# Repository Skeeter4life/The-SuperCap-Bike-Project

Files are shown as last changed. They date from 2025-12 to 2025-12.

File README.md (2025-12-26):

# SuperCAP V1 is Complete, and Deprecated in Light of V2.

## The Idea

I wanted an electric bike with a more dynamic feel than the typical e-bike; one in which you wouldn’t be able to get away with constantly cruising at 30km/h with minimal effort. I wanted an e-bike that had a sense of “sportyness”, quick, instantaneous acceleration. I also wanted the sence of scarcity. The goal was to have an e-bike that could get me up a hill, yet had limited capacity, such that it still enticed me to get some proper exercise. A super-capacitor based accumulator is perfect for this, as they have reduced charge density, and generally are able to source and sink signifigantly more current with less problems then for instance, a Lithium Ion battery. The accumulator would consist of two 12V 500F supercapacitor banks, which could be connected in parallel or in series. The electronics will be powered independently with a 12V battery.

> [!Note]
> These were my honest initial thoughts going into the project. The practical implications of this will be described in [Things That Went Wrong](#things-that-went-wrong)
>
> Inspiration  from [Tom Stanton's "Super Capacitor Bike"](https://www.youtube.com/watch?v=V_f8Q2_Q_J0) video on YouTube.

> [!Note]
> I am going to focus my discussion here on the hardware. There is so much to talk about regarding the firmware, but to keep this documentation of my learning as condensed as possible, I will rely on my comments I made in my code for you to interpret. 

> [!IMPORTANT]
> The uploaded schematic is original, and has NOT been updated to reflect any of the changes mentioned below. I have decided to use that time towards V2.

## Things That Went Right

### 1. Dedication and Perseverance
It is very important to know that I have had no formal education on any of this (as of 2025/11/08). I have not yet taken any course that explains the practical applications and operation of a diode, MOSFET, or any nonlinear device. I spent my evenings teaching myself as much as I could before falling asleep. I spent as much energy and time as I could during my free time (sometimes putting off homework…) to work on my project. I need to emphasize that I was extremely dedicated and determined to get this project in a usable state. I am only now taking ECE 370 this term, which sheds light on the operation of electromechanical devices.

I also did not have any adequate equipment when going into this project. I did not let that stop me, but reflecting back on it, it would have made a world of difference. Please, behold, the setup I had in my landlord’s garage while I was on co-op:

Setup-landlord

### 2. Decision to use a 2 Layer PCB for Prototyping
If you looked at this project in the early stages of development, you may remember that I chose the 2-layer PCB primarily due to cost and “EMI was not my primary concern” (Okay, that was really silly to say. Hindsight is 20/20). This will be briefly addressed in [Things That Went Wrong](#things-that-went-wrong), to an extent, as far as I can explain; I am not even close to being able to design for EMC. This choice ended up being quite beneficial as I needed to cut and re-route many, many traces on my PCB.

### 3. I had the Right Idea
I understood the principles of what needed to happen, and how it could be achieved. While some components could definitely have been chosen better ([Things That Went Wrong](#things-that-went-wrong)), atleast they were the correct type of components. I understood that I needed 3 half bridge circuits, one per phase. I understood that a P-type MOSFET typically has a higher $$R_{ds ON}$$ than an N-type MOSFET. I understood that I needed some sort of circuit to keep $$V_{gs}$$ in the saturation region as the high-side N-type MOSFET began to conduct. I understood the principles of decoupling capacitors, I choose appropriate values and kept them as close as possible to the IC. I even put bulk capacitance throughout my circuit (could have done a better job, but I will still give myself props). Furthermore, I even tried to put some (questionable at best) circuit protection features. This prototype defiently would not even be workable if I did not execute those parts properly.

## Things That Went Wrong 

As mentioned in [Things That Went Right](#things-that-went-right), I was completely self taught. I wish I had the time to learn absolutely  everything, tinker with each component for way longer, but things have been way too busy. Part of me just wanted this project done for the next co-op search and to finish my schoolwork, so, I rushed. There are many design flaws, logic errors, and inconsistencies throughout the project; but to keep this section concise and readable, I am going to limit myself and only discuss in detail the three most signifigant design faults. 

### 1. No ISP

This ultimately came down to an extremely silly error: I used 1.0mm header footprints, not 2.54mm. I had the pins to program the ATMEGA328P over UART, but due to their size, spacing, and my available tools, it made it way too finicky to solder on a bodge fix. As such, I had to remove the ATMEGA328P and place it onto a breadboard each time to reprogram, which is a mistake I do not want to repeat (The 28-PDIP IC defiently was not designed for constant insertion and removal). Additionally, my screw terminals were missing the SPI line MISO and a connection to the ATMEGA328p's RESET pin, so I had to repeat the process of removing the microcontroller each time to use DebugWIRE or change a fuse bit.

### 2. Chosen Components and Thermal Performance

I mentioned this before in [Things That Went Right](#things-that-went-right), that I did my best to figure out what all of the specifications meant on the datasheet, but it ultimetly meant that some paramaters got neglected. It is crazy to say, but sometimes I got so hooked after learning something nitty-gritty about a component, that I got excited and put it on my BOM, and completely neglected some other paramaters. For instance, let's take a look at my choice for using the onsemi 1N4148 signal diode [^5] used in the bootstrap circuit for the IR2104 [^30] (mistakenly, it has a schottky diode symbol on my schematic). 



The first thing that pops out to me is the absolute maximum recurrent peak forward current rating of 400mA. I likely exceed this during the initial C<sub>boot</sub> charging transient, as I do not have a current-limiting resistor in series with the diode. Below entails an analysis to see the current drawn at t = 0:

<p align="center">
  
$$ I(t) = I_oe^{\frac{-t}{\tau}} \text{ (A)}$$

$$ I(0) = I_o = V/R_{eq} \text{ (A)}$$

$$R_{eq} = R_{diode-eff} + Capacitor_{ESR} + Sourse_{ESR} + Parasitic_{ESR}\ (Ω)$$

Assumption: $$R_{diode-eff} = 0$$
I am assuming that the diode is an ideal diode to get an upper-bound for the peak surge current. There would be a forward voltage drop and some equivalent effective resistance at that current, but the datasheet does not provide any information as soon as the current $$> 800mA$$.

$$Capacitor_{ESR}: \ \approx \text{15 (mΩ)}$$

$$Sourse_{ESR}: \ \approx 8 * 0.2 = 1.6 \text{ (Ω) (8 1.5V AA alkaline batteries in series)} $$

$$Parasitic_{ESR}: \text{ The resistance of a trace with 1.5mm width, 0.6mm length, } 1 \frac{oz}{ft^2}, \text{ at } 25^{\circ}C \approx 0.194 \text{ (mΩ).}$$

IR2104 I/O impedence assumed neglegable.

$$R_{eq} \approx 1.62 \text{ (Ω)}$$

$$= 12/1.62 = 7.4 \text{ (A)}$$

</p>

However, the surge current decays quickly as seen at three time constants:

$$ I(t) = I_oe^{\frac{-t}{\tau}} \text{ (A)}$$

$$ I(3\tau) = \frac{I_o}{e^3} = V/(R * e^3) \text{ (A)}$$

$$= 12/32.54 = 369 \text{ (mA)}$$

Now let's take a quick look at its thermal characteristics:



It is quite likely I exceeded the power dissipation rating aswell. Now it is true that this tiny diode was dissipating power for a tiny amount of time: 

$$5\tau \text{ (s)} $$
$$\text{Voltage } C_{boot} = 0.993(12) \text{ (V)}$$
$$ = 5*RC_{boot} $$
$$ \text{= 5 * 1.62 * 0.000001 = 8.1 (us)} $$

So, it almost makes some sense that it did not explode as soon as I tried using my bootstrap circuit. The instantaneous power is quite high, but the average over time with the frequency I was switching the MOSFETs (~10kHz: a limitation of the timers in the ATMGEA328P) is acceptable. Nevertheless, its vital to design a system that meets all absoloute maximum ratings, with a buffer. 

Furthermore, The 1N4148 diode has a non-negligable forward drop when sinking even uA of current. The highside is still being driven at an appropriate $$V_{gs} \approx 11V$$. However, this is still worth additional consideration moving forward. 

<p align="center">

</p>

On the other hand, I do want to briefly go over the fact that the 1N4148 diode's maximum repetitive reverse voltage, reverse leakage current, reverse recovery time and junction capacitance specifications are appropriate for this use case. When the IR2104's high side gets switched on, the 1N4148 is going to need to handle a reverse voltage of 24V. It is rated for 100V, so that is a win. The only inductance in the loop is from the parasitics from the traces, so $$L \frac{di}{dt}$$ is small, and thus, the switching transient will remain well below 100V. The 1N914 has a reverse leakage of 0.025uA when $$V_R = 20V$$, which means I am not going to get too heavy in the math, but to my understanding, low leakage current means the bootstrap capacitor will stayed charged for longer, and the low junction capacitance/fast recovery time minimizes the ringing/switching loss, which is good.

I think that covers everything for the bootstrap diode. My math definitely overestimates the stress on the diode through my ideal diode simplification, but all in all, this is a better analysis than what I had before. If I were to choose any other component to replace it, under the following assumptions:

- Able to handle a repetitive surge forward current of a of couple amps, allowing for some $$C_{bs}$$ to be charged in the order of a few nanoseconds,
- Required reverse votlage of 24V * 2 (accumulator in series, 2* to give room for transients),
- Fast recovery time, minimizing losses
- Low leakage current
- Low forward voltage drop

I would choose [this Schottky diode](https://www.digikey.ca/en/products/detail/taiwan-semiconductor-corporation/SSH210H/18718578).

### 3. The MCP23017

To begin, a better choice would have been an I/O expander with a protocol capable of running at a higher baud rate, like SPI. One of my greatest mistakes in this project was not considering the timing implications of using the I/O expander, the MCP23017. I wired the digital output of hall effect sensors, break switches, and even the fault LED to the I/O expander. These are all things that I would want directly connected to the MCU. The hall and break switch interrupts are extremely high priority. The MCP23017 has two interrupt lines, multiplexed across the two ports, dedicating 8 independent pins per port. The designers of the MCP23017 added a register that holds the flags for the pins that raised an interrupt; however, this creates a major performance issue in my case. It is required to read the “interrupt captured register” before the interrupt line state resets. Every interrupt required a full read cycle, which is a major performance issue: the I2C bus for this application is unsafe, unreliable, and causes atleast a 10 times delay of the MCU’s ability to process subsequent interrupts. I originally did not consider this delay. As a result, the motor would stall at speed; the hall state would be read too late, and a phase with a lower index would be applied.

I did a brief analysis of how much time I had between subsequent hall states. Below is an image of the motor rotated to one of its commutation states:

<p align="center">

</p>

The radius I measured to be about $$50mm$$. Using a protractor, the rotor only needs to turn $$\approx 1^\circ$$ before the hall effect sensor changes state. The calculus for measuring the arc length of a circle has been done and is well known: 

$$L = 2\pi r \frac{\Theta}{360}$$

$$L \approx 0.87 \text{ mm}$$

Below is an image of the fastest possible I2C read transaction with the ATMEGA328P, 

(I consider this a feat, I am quite proud of this. Bit rate of ~1MHz (2f).

<p align="center">
SDS804X_HD_PNG_9
</p>

A bit of algebra yields the absolute maximum I2C interfaced motor speed:

$$\frac{0.87*10^{-3}}{v} \le (67.8 * 10^{-6}) + ISR_{execution} $$

$$\text{For simplicity (was not measured) } ISR_{execution} = 0$$

$$ v \le 12.8 \frac{m}{s} \approx 45 \frac{km}{h}$$

If you are familiar with I2C, you would have noticed that the ACK bit had a suspiciously high voltage. At the speeds I was running it, it would occasionally glitch and the MCP23017 would not be able to pull the ACK bit low, resulting in a NACK bit. Using stronger pull-up resistors did not make a noticeable difference. I was pushing the limits of my I2C bus, and the AMTEGA328p’s TWI timing capabilities; it is officially only rated for a 400kHz transfer speed.

So, when doing my tests, I reduced my I2C baud rate from 1MHz to 400kHz. Here is a video demonstrating the motor stalling (video is heavily compressed to meet 10MB upload limit, apologies):

https://github.com/user-attachments/assets/7227a615-8b7e-4955-889b-a2fbc8cb35df

> [!Note]
> I bought the oscilloscope and tools after my co-op. The PCB was designed and built at this time.

Revisiting the first note, the main flaw with this supercapacitor bike idea is that none of my electronics or even my motor is rated for large currents. I don’t have the datasheet for my motor (I asked, but, the seller wouldn’t give it to me), but the use of 16-gauge stranded aluminum phase wires was enough for me to realize that sinking anything around 10A was a bad idea. The other key flaw with my original intuition was I could simply just decided not use the e-bike’s power assist by turning it off, nullifying the entire supposed benefit of the limited capacity. Some sort of hybrid capacitor-battery approach would be better suited (Lithium-ion Capacitors), whilst keeping the spirit of the project.

### Honerable mentions:

**1. Incorrect Wiring of the IR2104's**
  - All shutdown pins were tied together.
    
**2. Completely Inconsistent Labels, Silkscreen, and Ordering**
  - MCP23017's INTA is labeled as INTB, and vice versa.
  - U2 has silkscreen "U1", U1 has silkscreen "U2".
  - U1, U2, and U3 are not organized in a sequential order.
  - Phase1, Phase2, and Phase3 connections are not listed sequentially.
    
**3. Wrong Footprints**
  - Barrel Jack (PJ-002AH) FootPrint: A lesson to not put complete trust into the EDA models found on DigiKey. I had ignored KiCAD's DRC violation that the hole clearance was 0mm, shorting supply and ground.
  - Relay (AWHSH105D00G) Footprints: Wrong footprint, one through-hole pad is entirely missing.
    
**4. Circuit Protection Elements Doing More Harm Than Good**
  - I have diodes on my 5V, 3.3V lines; this caused the voltage to be too close to $$V_{min}$$ of the MCP23017's defined logic levels.
    
**5. Schematic is Unorganized and Difficult to Read**
  - Organizing a schematic takes expereince.
    
**6. No (initial) Consideration of the I2C Bus Pull Up Resistors**
  - I arbitrarily chose 10kΩ, which I later had to add 2.2kΩ resistors in parallel.
    
**7. Series/Parallel Switching**
  - To keep this brief, I feel that this is still a good idea (assuming software and hardware has been implemented to ensure it is safe to do so), but there needs to be a major revision to what I have on my schematic. The most prominent issue is the relays. EMI was such an issue on my PCB that under high load, or some sort of grounding issue, the relay(s) would toggle. If I were to ever choose to use relays, I would need to do proper analysis to ensure that under no circumstances can they spuriously toggle. Also, I would need to add some sort of current sensing to ensure that I am still operating within the contact ratings. Another major concern is the potential for inrush currents. It is quite plausible to have one capacitor at a slightly different potential than the other. In addition to the current sensing, there would be a need for some sort of regulator to handle transients.
    
**8. I Did Not Add Any Real Way to Charge the Accumulator**
  - I had the original idea of just taking the accumulator off, hooking it up to a DC power supply etc, but a nice luxury would be to be able to plug it in directly to a wall outlet.

**9. The PCB Could Have Been Designed Better**
- I rushed the production of the PCB, and I believe I could have done a better job routing tracks and organizing the components. The ground and power planes are excessively fragmented, resulting in poor current return paths and increased noise.
- The board already exceeds the 100x100mm pricing tier. Surface mount components would have reduced cost and complexity. There is an excessive amount of signal via's, traces bending around IC's with sharp corners, etc., that could have been avoided with better component placement, organization and additional board space. Additionally, I would have been able to better separate the sensitive digital electronics from any high power tracks and the power plane. 
-  I could have improved thermals and reduced capacitive coupling with the use of thermal and stitching vias. Furthermore, I should have kept the high-frequency SPI, I2C, and the crystal oscillator tracks as isolated, short, and straight as possible.
    
**10. No Pull-Down Resistors on Some MOSFETS**
  - I did not add any pulldown resistors on the half-bridge FET's. When the IR2104 driver was in a HIGH-Z state, capacitive coupling caused $$V_{gs}$$ to increase, just enough to start to put the FET into conduction. The only reason I noticed this is because some FET's got mysteriously hot.
    
**11. Bootstrap resistors, Gate Resistors Chosen Arbitrarily**
  - To be fair to myself, I had no equipment at the time to be able to emperically measure the effects of one gate resistor vs. another. However, these are the sorts of things you can get an upper and lower bound for through calculations, which I did not do.

There are definitely some more things I did not write, might have missed/don't fully understand yet. All in all, I will conclude this section here, as I believe it highlights the core of my learning. If there is something here you would like to talk about, feel free to in an interview or in the issues section.

## The Outcome

I consider this project to be a success. I had a lot of fun releasing some magic smoke. In all seriousness, I got some incredibly valuable hands on experience designing my first ever prototype for quite an ambitious project. I essentially have a fully functional BLDC motor controller. Below, I posted an uncompressed video of one of the "top speed" runs of my motor (or at least, as fast as I can go without feeling worried about tripping my room's breaker or melting those aluminum wires).

<div align="center">
  <video src="https://github.com/user-attachments/assets/f553f186-a5bf-4020-b508-6ff7d6a13e7c">
</video>
</div>

(Note: I was using a higher duty cycle than the I2C test) Below is an image of the bottom my PCB with the "bodge" fixes:

<p align="center">
PCB_Bodge
</p>

Below is a top down view of the PCB:

<p align="center">
PCB_Bodge
</p>

## What I Will do in Version 2

Version 2 will address all of the aforementioned issues. Here are my initial thoughts and goals:

- I will switch to a more capable microcontroller. I am definitely looking into STM32, I need something with a higher instruction throughput, greater word size, ideally has an FPU, variable frequency timers (capable of field-oriented control), and more I/O. Everything should be able to interface directly to the MCU. I need to include relevant ISP modules.
- I need to switch to a larger 4-layer or 6-layer PCB, and improve my designs layout and organization. I will attempt to reduce EMI: I should have dedicated uninterrupted ground planes, stitching vias, and use best practices to keep high-frequency traces short and straight. I also need to keep thermals in mind.
- I will use heat sinks where needed and thermal vias; stitching the top and bottom copper planes.
- I will perform power and EMI analysis (I will be switching to Altium).
- I will design a proper back-EMF circuit for regenerative braking; power dissipation in body diodes will be high and inefficient.
- I will switch to a Li-ion capacitor-based accumulator. I will design a circuit to allow for charging directly from a standard wall outlet. This of course requires safe charging/protection features.
- I will design a current and voltage monitoring system to ensure the motor is operating safely, and to take action when it is not.
- I will aim to drive a 500W BLDC motor (a motor *with* a datasheet). I will consider the motor's characteristic curves to maximize power output and efficiency.

## Bill of Materials

Ceramic Capacitors: 
- 0.1uF x 7 [^1], 
- 0.33uF x 2 [^2],
- 1uF x 3 [^3]

Electrolytic capacitors: 
- 10uF x 4 [^4]
  
Diodes:
- 1N4148 x 3 [^5], 
- 1N5819 x 5 [^6]

LEDs: 
- 5.0mm THT x2 [^7]

Fuse: 
- 0225002.MXP x1 [^8], *Note:* Never implemented or tested.
- F4658-ND x 1 [^9] *Note:* Never implemented or tested.

Sockets & Pins: 
- 1x01 1.00mm Vertical Male Pin x 5 [^10],  *Note:* Never purchased, implemented or tested.
- 8 Dip 7.62mm Socket x 5 [^11],
- 16 Dip 7.62mm Socket x 1 [^12], 
- 28 Dip 7.62mm Socket x2 [^13] 

Barrel Jack: 
- PJ_002AH x 1 [^14]

Relays: 
- AWHSH105D00G x 2 [^15]

MOSFETS:
- IRFZ44N x 7 [^16], 
- GT065P06T x 1 [^17]

Resistors: 
- 0Ω, 10Ω, 220Ω, 10kΩ, 22kΩ Resistor Kit: [^18]

Terminals: 
- 1988804 x 1 [^19], 
- 1988817 x 2 [^20], 
- 1190363 x2  [^21], 
- 1988862 x 3 [^22]

Microprocessors: 
- ATMEGA328P x 1 [^23]

Crystal Oscillator: 
- MXO45HS-3C-20M000000 x 1 [^24]

GPIO Expander: 
- MCP23017 x 1 [^25]

Button: 
- TS02-66-50-BK-160-LCR-D x 1 [^26]

MOSFET Gate Driver: 
- UCC37324P x 1 [^27] *Note:* Never implemented.

Darlington Transistors Array: 
- ULN2003 x 1 [^28]

Digital Potentiometers: 
- MCP4151 x 1 [^29]

Half Bridge Drivers: 
- IR2104 x 3 [^30]

Linear Regulators: 
- L7805 x1 [^31], 
- L78L33ACZ x1 [^32] *Note:* Never purchased, implemented or tested.

Hall Effect Sensors: 
- TMAG5213AGQLPG x 3 [^33]

Switches: 
- 2057-SW-R-K1-A-ND x 1 [^34] 

Subtotal: **$ 146.17 CAD** (as of 2025/11/08)

## Schematic and PCB

### Schematic:  

  To reduce image congestion, please clone the repository and access the schematic on KiCAD version 8+.

### PCB:

<div align="center">

PCB_Components
PCB_Traces

</div>

## My Policy on the Use of AI

I fully acknowledge the emergence of AI and how useful it can be as a tool. However, I am also fully aware that there are negative consequences for the overreliance on AI. That being said, I take pride in the fact that I fully wrote all core components of my code; the same is said with the hardware portion. If you look carefully through my program, you will be able to pick up my quirks and coding style. However, I did not completely abstain from using AI. I would ask ChatGPT to help me with a concept, look up what register to use, or how to perform some sort of function. I used ChatGPT as a tutor, not as a tool to do everything for me. It is worth mentioning that ChatGPT is not perfect. For instance, I pasted some code into ChatGPT and asked “what interrupt vector do I use here?”, to which ChatGPT said “INT_vect” instead of “INT0_vect”. A very minor mistake, but I didn’t understand what was wrong, and I was using no other resources. I was then confused for an hour about why my ISR never executed. It was confidently incorrect the entire time we went through the debugging process; I was overreliant, and ChatGPT was more concerned with my wiring setup than realizing the interrupt vector was wrong. So, to summarize, AI is a great tool, and there are parts of my code where AI helped me out, but I never just blindly copied and pasted big chunks of its work for a full feature. I spent countless hours going through datasheets (I feel like I am one of the very few people who have read nearly the entirety of the ATMEGA328P datasheet), did my best to find information myself, and then, if all else failed, I would have asked ChatGPT for some advice.

<div align="center">

  ***Thank you!***

</div>

Hall-Effect-Sensor-Replacement

## Links

[^1]: https://www.digikey.ca/en/products/detail/kemet/C322C104M5U5TA/818107
[^2]: https://www.digikey.ca/en/products/detail/kemet/C330C334M5R5TA/6562403
[^3]: https://www.digikey.ca/en/products/detail/kemet/C330C105K5R5TA7301/3726162
[^4]: https://www.digikey.ca/en/products/detail/cornell-dubilier-knowles/106CKE400M/5410625
[^5]: https://www.digikey.ca/en/products/detail/onsemi/1N4148/458603
[^6]: https://www.digikey.ca/en/products/detail/stmicroelectronics/1N5819/1037326
[^7]: https://www.digikey.ca/en/products/detail/marktech-optoelectronics/MT4118-HR-A/4214622
[^8]: https://www.digikey.ca/en/products/detail/littelfuse-inc/02540101Z/553102
[^9]: https://www.digikey.ca/en/products/detail/littelfuse-inc/0225002-MXP/777781
[^10]: https://www.digikey.ca/en/products/detail/samtec-inc/TS-101-T-A/1105493
[^11]: https://www.digikey.ca/en/products/detail/te-connectivity-amp-connectors/1-2199298-2/5022039
[^12]: https://www.digikey.ca/en/products/detail/on-shore-technology-inc/ED16DT/4147596
[^13]: https://www.digikey.ca/en/products/detail/adam-tech/ICS-328-T/9832859
[^14]: https://www.digikey.ca/en/products/detail/same-sky/PJ-002AH/408446
[^15]: https://www.digikey.ca/en/products/detail/amphenol-anytek/AWHSH105D00G/16721986
[^16]: https://www.digikey.ca/en/products/detail/umw/IRFZ44N/24889964
[^17]: https://www.digikey.ca/en/products/detail/goford-semiconductor/GT065P06T/18088004
[^18]: https://www.digikey.ca/en/products/detail/sparkfun-electronics/COM-10969/14671649
[^19]: https://www.digikey.ca/en/products/detail/phoenix-contact/1988804/950892
[^20]: https://www.digikey.ca/en/products/detail/phoenix-contact/1988817/950893
[^21]: https://www.digikey.ca/en/products/detail/phoenix-contact/1190363/14680902
[^22]: https://www.digikey.ca/en/products/detail/phoenix-contact/1988862/950898
[^23]: https://www.digikey.ca/en/products/detail/microchip-technology/ATMEGA328P-PN/2357094
[^24]: https://www.digikey.ca/en/products/detail/cts-frequency-controls/MXO45HS-3C-20M000000/1801871
[^25]: https://www.digikey.ca/en/products/detail/microchip-technology/MCP23017-E-SP/894272
[^26]: https://www.digikey.ca/en/products/detail/same-sky-formerly-cui-devices/TS02-66-50-BK-160-LCR-D/15634352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
[^27]: https://www.digikey.ca/en/products/detail/texas-instruments/UCC37324P/571464
[^28]: https://www.digikey.ca/en/products/detail/stmicroelectronics/ULN2003A/599603
[^29]: https://www.digikey.ca/en/products/detail/microchip-technology/MCP4151-103E-P/1874217
[^30]: https://www.digikey.ca/en/products/detail/infineon-technologies/IR2104PBF/812198
[^31]: https://www.digikey.ca/en/products/detail/stmicroelectronics/L7805CV/585964
[^32]: https://www.digikey.ca/en/products/detail/stmicroelectronics/L78L33ACZ/1038304
[^33]: https://www.digikey.ca/en/products/detail/texas-instruments/TMAG5213AGQLPG/22531584
[^34]: https://www.digikey.ca/en/products/detail/adam-tech/SW-R-K1-A/15284469

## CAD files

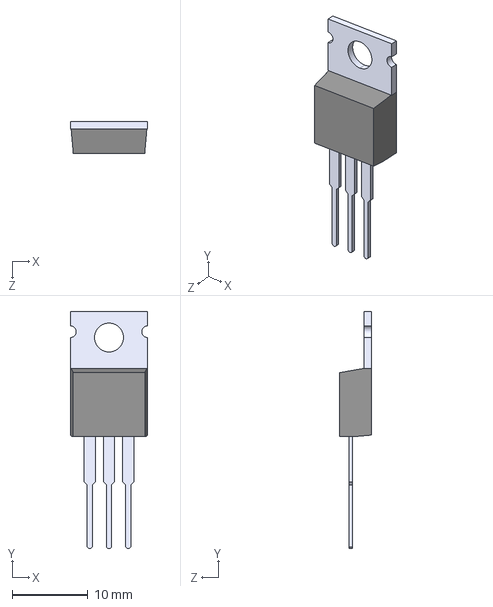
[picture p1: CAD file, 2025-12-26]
Hardware/Libraries_Kicad/Footprints/IRFZ44N/IRFZ44N.step
10.2 x 31.2 x 4.19 mm

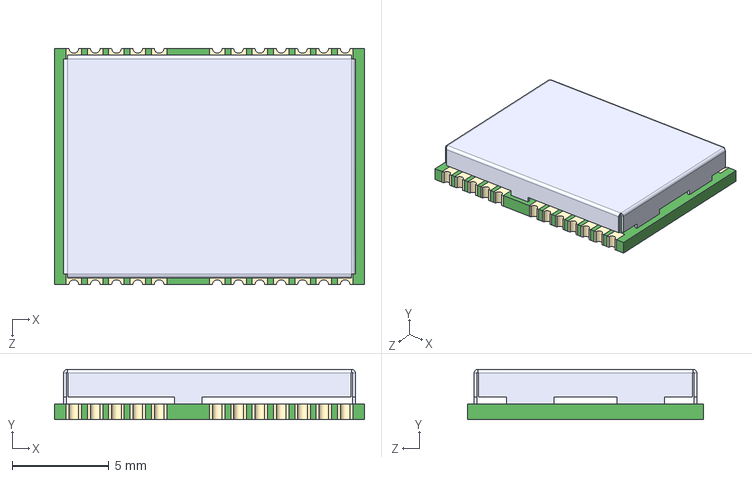
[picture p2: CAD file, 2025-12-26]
Hardware/Libraries_Kicad/Footprints/NEO/NEO-M8N-0.step
16.0 x 2.60 x 12.2 mm

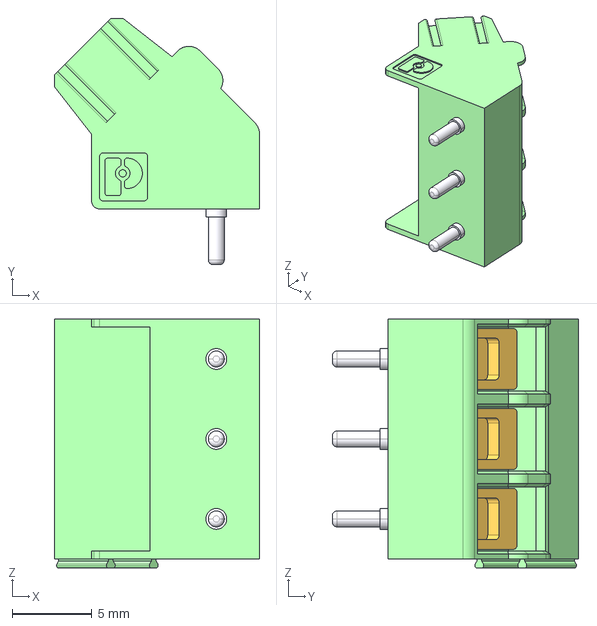
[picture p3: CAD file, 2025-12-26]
Hardware/Libraries_Kicad/Footprints/Terminal_1988817/1988817.step
12.8 x 15.4 x 15.6 mm

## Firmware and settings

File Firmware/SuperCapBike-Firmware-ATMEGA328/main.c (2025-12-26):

/*
 * main.c
 *
 *  Author: Andrew
 */ 

//------- Includes:
#include "Headers/Includes.h"
#include "Headers/EEPROM.h"
#include "Headers/Timer_Counter.h"
#include "Headers/Dynamic_Ring_Buffer.h"
#include "Headers/I2C.h"
#include "Headers/Motor_Driver.h"

const uint32_t F_CLK = 20000000;
const uint32_t TC_CLK = 20000000; // TC_CLK (timer counter) can be asynchronous to F_CLK.

// Interesting note here: TC_CLK = F_CLK will not compile.

const Timers Global_Timer = _8_bit2;

Ring_Buffer* p_TWI_Buffer;

int main(void)
{
	sei(); // Enable global interrupts
	
	MCUCR |= (1 << PUD); // Disable pull up resistors
	
	Timer_Status Timer1_Set = Configure_Timer(1, u_MiliSeconds, Global_Timer); // 8 bit2 is free in my case, not needed for PWM
	
	if(!Timer1_Set){
			
		Error_Log Timer_Error = {
			.Message = "TIMER1",
			.Time = 0
		};
			
		Log_Error(&Timer_Error);
			
	}
	
	//TWI_Write(MCP23017_Address, 0x00, 0b11101111); 
	//TWI_Write(MCP23017_Address, 0x14, 0b00010000); // Turn on fault led
	
	Motor_Status Motor_Setup = Init_Motor();
	
	if(Motor_Setup == Motor_FAULT) return 1;

	
	//DDRB |= (1 << DDB0) | (1 << DDB1) | (1 << DDB2) | (1 << DDB3);
	//DDRD |= (1 << DDD6)| (1 << DDD7) | (1 << DDD5) | (1 << DDD3);
	
	//
	//
	//Timers Timer2 = _8_bit1;
	//
	//Timer_Status Timer2_Set = Configure_Timer(5000, u_MicroSeconds, Timer2);
	//
	//Timers Timer3 = _16_bit;
	//
	//Timer_Status Timer3_Set = Configure_Timer(3, u_Seconds, Timer3);
	//
	//PWM_Setup Phase1;
	//
	//Phase1.Pin = PD5_OC0B;
	//
	//Timer1_Set = Init_PWM(&Phase1);
	//
	//Configure_PWM(&Phase1, 1, 50);
	//
	//if(!Timer1_Set || !Timer2_Set || !Timer3_Set){
		//PORTB = (1 << PORTB1);
	//}
		//
	///*
	//int16_t W1 = EEPROM_Write(0x0000, 0x1C);
	//
	//int16_t R1 = EEPROM_Read(0x0000);
	//
	//int16_t W2 = EEPROM_Write(0x0001, 0x1D);
		//
	//if(!W1 || !W2 || !R1){
		//PORTB = (1 << PORTB1);
	//}*/
		//
	//uint8_t Received_Data = 0;
	//
	Ring_Buffer TWI_Buffer;
	Ring_Buffer* p_TWI_Buffer = &TWI_Buffer; 
	
	TWI_Buffer_Enabled = true;
	
	Init_Buffer(p_TWI_Buffer, 25, 25);
	
	//TWI_Add_W_To_Queue(p_TWI_Buffer, MCP23017_Address, 0x01, 0b11111111);// Non imperative TWI operations. Only allowable under a certain speed.
	//TWI_Add_R_To_Queue(p_TWI_Buffer, MCP23017_Address, 0x13, &Received_Data);
	
	//TWI_Read(MCP23017_Address, 0x00, &Received_Data, NULL);
	
	while(1){
		
		//if(TWI_Buffer_Enabled && Current_Speed <= 20 && !IsEmpty(p_TWI_Buffer) && Next_I2C_State == TWI_IDLE){
			//Fetch_TWI(p_TWI_Buffer);
		//}

		
	}
	
	Free_Buffer(p_TWI_Buffer); // Needs to exist for the entire duration of the program.
	
	//while (1 == true){
		//
		//if(TWI_Ready == true){
			//
			//TWI_Handler(&MCP23017);
			//
		//}
	//
	//} // Part of TWI_Old
	
	return 0;
}

/*
avrdude -c usbtiny -p m328 -U ?:?:"C:\Users\Andrew\Documents\SuperCap_Bike\SuperCapBike-Software\SuperCapBike-Firmware-ATMEGA328\Debug\SuperCapBike-Firmware-ATMEGA328.hex":?
*/

/*
cd C:\Users\Andrew\Documents\SuperCap_Bike\SuperCapBike-Software\SuperCapBike-Firmware-ATMEGA328
*/

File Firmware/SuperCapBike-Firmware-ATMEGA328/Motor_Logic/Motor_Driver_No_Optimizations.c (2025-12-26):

/*
 * Motor_Driver.c
 *
 *  Author: Andrew
 */ 


// Phase angle: 120 degrees


#include "../Headers/Includes.h"
#include "../Headers/I2C.h"
#include "../Headers/Motor_Driver.h"
#include "../Headers/Timer_Counter.h"

volatile uint8_t Current_Speed = 0;
volatile Accumulator_State Switching_State = Parallel;

volatile uint8_t Hall_State = 0;
volatile TWI_Status Status;

uint8_t Duty_Cylce = 82;
// uint8_t PWM_Prescaler = 8;

volatile bool Commutation_Busy = false;

volatile bool Motor_Enabled = true; // Some things are volatile because I may use them in an ISR and would rather not forget to make it volatile. Ill optimize once everything works.

PWM_Setup IN_1;
PWM_Setup IN_2;
PWM_Setup IN_3; // Could just use the pins locally for each function, but this makes things a bit more cohesive 

#define SD_U1 PORTD0
#define SD_U2 PORTD4
#define SD_U3 PORTD1

#define IN1_PIN PD6  // U2
#define IN2_PIN PD5  // U1
#define IN3_PIN PB1  // U3

void Update_Commutation(void);

// IN_2 -> P2 IN_1 -> P1 IN_3 -> P3

// In2 and In1 share the same timer

ISR(PCINT0_vect){ // Port B PCINT ISR
	
	Hall_State = ((PINC & (1 << PINC3)) >> 1) | ((PINB & (1 << PINB7)) >> 6)  | ((PINB & (1 << PINB2)) >> 2);
	Update_Commutation(); // Time critical task. Appropriate to do in ISR. Like literally the #1 thing it has to do quickly.

}

ISR(PCINT1_vect){ // Port C PCINT ISR

	Hall_State = ((PINC & (1 << PINC3)) >> 1) | ((PINB & (1 << PINB7)) >> 6)  | ((PINB & (1 << PINB2)) >> 2);
	Update_Commutation(); 

}

void Update_Commutation(void){
	
	if(!Motor_Enabled) return;
	
	//TWI_Write(MCP23017_Address, 0x00, 0b11101111);
	//TWI_Write(MCP23017_Address, 0x14, 0b00010000); // Turn on fault led
	
	const Phase_Logic Commutation_LUT[8] = {
		[0b000] = { Phase_Invalid, Phase_Invalid, Phase_Invalid }, // invalid

		[0b001] = { Phase_B, Phase_C, Phase_A }, // Hall 001 -> B+, C-, Az
		[0b010] = { Phase_C, Phase_A, Phase_B }, // Hall 010 -> C+, A-, Bz
		[0b011] = { Phase_B, Phase_C, Phase_A }, // Hall 011 -> B+, C-, Az

		[0b100] = { Phase_A, Phase_B, Phase_C }, // Hall 100 -> A+, B-, Cz
		[0b101] = { Phase_A, Phase_B, Phase_C }, // Hall 101 -> A+, B-, Cz // Skip?
		[0b110] = { Phase_A, Phase_B, Phase_C }, // Hall 110 -> A+, B-, Cz

		[0b111] = { Phase_Invalid, Phase_Invalid, Phase_Invalid }  // invalid

	};
	
	if(Commutation_Busy == true){
		
		Error_Log Motor_Error = {
			
			.Message = "MOTOR",
			.Time = Global_Timer
			
		};
		
		Log_Error(&Motor_Error);
		
		EICRA &= ~(1 << ISC01); // Disable INT0
		
		PORTD &= ~((1 << SD_U1) | (1 << SD_U2) | (1 << SD_U3)); // Ensure all IR2014's are in shutdown state
		
		Motor_Enabled = false;
		
		return;
		
	}
	
	Commutation_Busy = true;
	
	
	// Error state -> Will add error flag and error handling
		
	// ^ Yeah this really slows things down. Design mistake.
	
	uint8_t Phase_Index = Hall_State; // Used to be different. 
	
	if(Phase_Index == 7 || Phase_Index == 0){
		
		Error_Log Motor_Error = {
			
			.Message = "MOTOR H",
			.Time = Global_Timer
			
		};
		
		Log_Error(&Motor_Error);
		
		PCMSK0 &= ~(1 << PCINT2); // Disable PCINT2
			
		PCMSK1 &= ~(1 << PCINT11);
		
		PORTD &= ~((1 << SD_U1) | (1 << SD_U2) | (1 << SD_U3)); // Ensure all IR2014's are in shutdown state
		
		Motor_Enabled = false;
		
		return; 
	}
			
	const Phase_Logic* Current_Phase = &Commutation_LUT[Phase_Index]; // Not checking for out of bounds. Mask GPB5-3.
		
	// Phase A is IN_1 or U2, Phase B is IN_2 or U1, Phase C is IN_3 or U3
	
	switch(Current_Phase->High){ // Reminder: IN1 and IN2 share the same timer. Changing 
		
		case Phase_A:
		
			Toggle_PWM(&IN_1, ON);
			DDRD |= (1 << DDD6); // IN1 as output (U2)
			
			break;
		
		case Phase_B:
			
			Toggle_PWM(&IN_2, ON);
			DDRD |= (1 << DDD5); // IN2 (U1)
			
			break;
			
		case Phase_C:
			
			Toggle_PWM(&IN_3, ON);
			DDRB |= (1<< DDB1); // IN3 (U3)
			
			break;
			
		default:
		
			return; // Error state
			
	}
	
	switch(Current_Phase->Low){
		
		case Phase_A:
		
			Toggle_PWM(&IN_1, OFF); // Note: if the COMnX bit(s) are set, the functionality of the PORTx register is overridden
			
			PORTD &= ~(1 << PORTD6); // IN1 digital LOW
			
			DDRD |= (1 << DDD6); // Set output
		
			break;
		
		case Phase_B:
		
			Toggle_PWM(&IN_2, OFF);
			
			PORTD &= ~(1 << PORTD5); // IN2 digital LOW
			
			DDRD |= (1 << DDD5);
					
			break;
		
		case Phase_C:
		
			Toggle_PWM(&IN_3, OFF);
			
			PORTB &= ~(1 << PORTB1); // IN3 digital LOW
			
			DDRB |= (1 << DDB1);
					
			break;
		
		default:
		
			return; // Error state
		
	}
	
	switch(Current_Phase->High_Z){ 
		
		case Phase_A: // Shutdown U1 IR2104
			
			// Toggle_PWM(&IN_1, OFF); 
			
			PORTD &= ~(1 << SD_U2); // SD U2 (Phase A)

			DDRD &= ~(1 << DDD6); // IN1 as an input			
			PORTD |= (1 << SD_U1) | (1 << SD_U3); // Enable PhaseB (IN2), PhaseC (IN3)

			break;
			
		case Phase_B: // Shutdown U2 
			
			// Toggle_PWM(&IN_2, OFF); 
			 
			PORTD &= ~(1 << SD_U1); // SD U1 (Phase B)
			
			DDRD &= ~(1 << DDD5); // IN2 as input
			
			PORTD |= (1 << SD_U2) | (1 << SD_U3); // Enable PhaseA, PhaseC
			
			break;
				
		case Phase_C: // Shutdown U3
			
			// Toggle_PWM(&IN_3, OFF);   
			
			PORTD &= ~(1 << SD_U3); // Shutdown U3 (Phase C)
			
			DDRB &= ~(1 << DDB1); // IN_3 as an input
	
			PORTD |= (1 << SD_U1) | (1 << SD_U2); // Enable PhaseA, PhaseB
			
			break;
			
		default:
		
			return; // Error state
			
	}
	
	Commutation_Busy = false;
	
	return;
}
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

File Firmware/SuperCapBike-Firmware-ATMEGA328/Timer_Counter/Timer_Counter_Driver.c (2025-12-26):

/*
 * Timer_Counter_Driver.c
 *
 * Author : Andrew
 */ 

// Note/Reminder: The constexpr keyword was not added until the C23 standard
// Some may find my commenting superfluous, but I just want to make sure I am being clear... :)

#include "../Headers/Includes.h"
#include "../Headers/Timer_Counter.h"

volatile uint64_t System_Ticks[3] = {0, 0, 0}; // Each tick is defined by Configure_Timer
volatile uint32_t Calculated_Ticks[3] = {0, 0, 0};
volatile uint32_t Remaining_Ticks[3] = {0, 0, 0};
	
Timer_Modes Timer_Mode[3] = {TIMER_NONE, TIMER_NONE, TIMER_NONE};
Timer_Units Timer_Unit[3] = {Invalid, Invalid, Invalid}; // Excuse my inconsistent use of caps lock lol. Ill fix that eventually.
uint16_t Timer_Step[3] = {0, 0, 0};
	
Timers Selected_Timer = TIMER_NONE;

//------- Timer Definitions:

const uint8_t Max_ISR_Cycles = 150; // Max time the ISR will take to increment System_Ticks.

ISR(TIMER0_COMPA_vect){
		
	if(Remaining_Ticks[_8_bit1] == 0){
		
		//PORTD ^= (1 << PORTD6);
				
		if(Calculated_Ticks[_8_bit1] > 0){
			
			Remaining_Ticks[_8_bit1] = Calculated_Ticks[_8_bit1]; // Reset the counter
			OCR0A = 0xFF;
			
		}
		
	}else{

		uint8_t NextOCR = (Remaining_Ticks[_8_bit1] > 0xFF) ? 0xFF : (uint8_t)Remaining_Ticks[_8_bit1];

		OCR0A = NextOCR;
		Remaining_Ticks[_8_bit1] -= NextOCR;
		
	}
	
}

ISR(TIMER2_COMPA_vect){
	
	if(Remaining_Ticks[_8_bit2] == 0){
		
		//PORTD ^= (1 << PORTD7);
		
		System_Ticks[_8_bit2]++; 

		if(Calculated_Ticks[_8_bit2] > 0){
			
			Remaining_Ticks[_8_bit2] = Calculated_Ticks[_8_bit2]; 
			OCR2A = 0xFF;
			
		}
		
	}else{

		uint8_t NextOCR = (Remaining_Ticks[_8_bit2] > 0xFF) ? 0xFF : (uint8_t)Remaining_Ticks[_8_bit2];

		OCR2A = NextOCR;
		Remaining_Ticks[_8_bit2] -= NextOCR;
		
	}

}


ISR(TIMER1_COMPA_vect){
	
	if(Remaining_Ticks[_16_bit] == 0){
		
		//PORTB ^= (1 << PORTB0);
		
		System_Ticks[_16_bit]++;
		
		if(Calculated_Ticks[_16_bit] > 0){
			
			Remaining_Ticks[_16_bit] = Calculated_Ticks[_16_bit];
			OCR1AH = 0xFF;
			OCR1AL = 0xFF;
			
		}
		
	}else{
		
		uint16_t NextOCR = (Remaining_Ticks[_16_bit] > 0xFFFF) ? 0xFFFF : (uint16_t)Remaining_Ticks[_16_bit];
		
		OCR1A = NextOCR;
		Remaining_Ticks[_16_bit] -= NextOCR;
		
	}
	
}

static Timer_Status Set_Prescaler(Timers Timer, uint16_t Prescaler){
	
	switch(Timer){
		
		case _16_bit:
		
			TCCR1B &= ~((1 << CS12) | (1 << CS11) | (1 << CS10)); // Clear previous prescaler bits
				
			switch(Prescaler){ // Don't need to clear TCCRxB, as it will be assigned:
				
				case 1:
				
					TCCR1B |= (1 << CS10);
					break;
				
				case 8:
					
					TCCR1B |= (1 << CS11);
					break;
				
				case 64:
				
					TCCR1B |= (1 << CS11) | (1 << CS10);
					break;
					
				case 256:
				
					TCCR1B |= (1 << CS12);
					break;
				
				case 1024:
				
					TCCR1B |= (1 << CS12) | (1 << CS10);
					break;
				
				default:
				
					return TIMER_FAULT;
				
			}
			
			break;
		
		case _8_bit1:
		
			TCCR0B &= ~((1 << CS02) | (1 << CS01) | (1 << CS00));
		
			switch(Prescaler){
				
				case 1:
				
					TCCR0B |= (1 << CS00);
					break;
				
				case 8:
				
					TCCR0B |= (1 << CS01);
					break;
				
				case 64:
				
					TCCR0B |= (1 << CS01) | (1 << CS00);
					break;
				
				case 256:
				
					TCCR0B |= (1 << CS02);
					break;
				
				case 1024:
				
					TCCR0B |= (1 << CS02) | (1 << CS00);
					break;
				
				default:
				
					return TIMER_FAULT;
				
			}
			
			break;
		
		case _8_bit2:
		
			TCCR2B &= ~((1 << CS22) | (1 << CS21) | (1 << CS20));
		
			switch(Prescaler){
				
				case 1:
				
					TCCR2B |= (1 << CS20);
					break;
				
				case 8:
				
					TCCR2B |= (1 << CS21);
					break;
				
				case 64:
				
					TCCR2B |= (1 << CS22);
					break;
				
				case 256:
				
					TCCR2B |= (1 << CS22) |  (1<<CS21);
					break;
				
				case 1024:
				
					TCCR2B |= (1 << CS22) | (1 << CS21) | (1 << CS20);
					break;
				
				default:
								
					return TIMER_FAULT;
				
			}
			
			break;
		
		default:
		
			return TIMER_FAULT;
	}
	
	return TIMER_OK;
	
}


Timer_Status Configure_Timer(uint16_t Step, Timer_Units Unit, Timers Selected_Timer){ // All relevent types were optimized by calculating the largest possible values to Configure_Timer_Step()
	
	if(TC_CLK == 0){ 
		return TIMER_FAULT;
	}
	
	if(Unit == 0){
		return TIMER_FAULT;
	}
	
	if((uint64_t)TC_CLK * Step/Unit <= Max_ISR_Cycles){ // If the requested tick is shorter than or equal to the max time it takes to increment System_Ticks, return error state
		return TIMER_FAULT;
	}
	
	//uint32_t Adjusted_Cycles = 0; // Won't overflow even with a 1Hz clock

	/*
	if(F_CLK >= TC_CLK){
		// Having this opens the door to the question: Consistency or precision?
		Adjusted_Cycles = ((F_CLK + (TC_CLK/2))/TC_CLK) * Avg_ISR_Cycles;
	}else{
		Adjusted_Cycles = ((TC_CLK + (F_CLK/2))/F_CLK) * Avg_ISR_Cycles;
	} */

	uint64_t Numerator = Step * TC_CLK;
	uint64_t Scaled_Ticks = Numerator / Unit; // How many times we have to count for the requested time to have passed at the current clock frequency
	
	uint16_t Prescaler = 0;
	uint32_t Calculated_Prescaler = 0; // Ensures that OCRxA is <= (2^n - 1)
		
	switch(Selected_Timer){
		
		case _16_bit:
			
			TIMSK1 = TIMSK1 & ~(1 << OCIE1A); // Disable the timer interrupt as it is being reconfigured.

			Calculated_Prescaler = (Scaled_Ticks+65534)/65535; // Ceiling function

			break;
		
		case _8_bit1:
			
			TIMSK0 = TIMSK0 & ~(1 << OCIE0A);
			
			Calculated_Prescaler = (Scaled_Ticks+254)/255;
			
			break;
			
		case _8_bit2:
			
			TIMSK2 = TIMSK2 & ~(1 << OCIE2A);
			
			Calculated_Prescaler = (Scaled_Ticks+254)/255;
		
			break;
			
		default:
		
			return TIMER_FAULT;
		
	}


	if(Calculated_Prescaler > 1024){  // The required count will overflow the selected timer, even with the largest available prescaler

		Prescaler = 1024;
		
		//Adjusted_Cycles = (((TC_CLK + (F_CLK*Prescaler/2))/F_CLK*Prescaler) * Avg_ISR_Cycles); // I may revisit this. Quite challenging to get right, and even harder to get consistently right
		
		Calculated_Ticks[Selected_Timer] = (Scaled_Ticks >> 10);
		
		Remaining_Ticks[Selected_Timer] = Calculated_Ticks[Selected_Timer];
		
		switch(Selected_Timer){
			
			case _16_bit:
				
				TCCR1B = (1 << CS12) | (1 << CS10) | (1 << WGM12); // Set prescaler to 1024, CTC mode (TCCR = Timer counter control register)
								
				OCR1AH = 0xFF;
				OCR1AL = 0xFF; // Timer begins
				
				TIMSK1 = (1 << OCIE1A); // Timer/Counter1 Interrupt Mask Register -> Enabled interrupt for progrm at TIMER1_COMPA_vect to be executed on compare match
				break;
			
			case _8_bit1:
				
				TCCR0A = (1 << WGM01);
				TCCR0B = (1 << CS02) | (1 << CS00);
				
				TIMSK0 = (1 << OCIE0A);
				
				OCR0A = 0xFF;
				break;
			
			case _8_bit2:

				TCCR2A = (1 << WGM21);
				TCCR2B = (1 << CS22) | (1 << CS21) | (1 << CS20);
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
